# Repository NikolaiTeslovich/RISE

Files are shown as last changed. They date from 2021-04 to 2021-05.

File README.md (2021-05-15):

<h1 align="center">
  The Rocket Lab Initiative — RISE
</h1>

<p align="center">
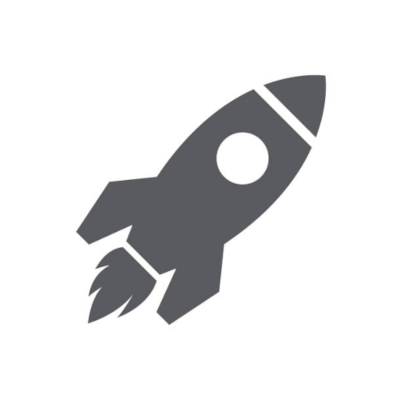
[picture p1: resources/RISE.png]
  
</p>

<p align="center">
  <a href="https://github.com/NikolaiTeslovich/RISE/blob/main/LICENSE">
    
  </a>
</p>

<p align="center">
  A payload that collects data and video throughout the flight of a model rocket.
</p>

# To do

- find appropriate camera resolution and framerate, [here's a helpful article](https://picamera.readthedocs.io/en/release-1.10/fov.html)
  - the spycam is the same as the picamera v1
  - does this affect the rate of data collection?
- Error encountered involving duplicate values with the data collections for the index
  - Meaning that 200 and 201 have the same time value, and are duplicates

# Breakdown of the code

1. First it imports the packages, sets up the sensors over I2C, and starts recording video.
2. Creates a new directory to put the data and video into, to prevent overwriting any data.
    - If no data directories exist, create the `data1` directory.
    - If the `data1` directory already exists, create the `data2` directory, etc.
3. Waits until the `delay_time` is over to collect data from the sensors as fast as possible using a [NumPy](https://numpy.org/) array over the `record_time` interval.
    - This comes out to about 40 measurements/sec compared to ~10 measurements/sec if I had used [pandas](https://pandas.pydata.org/) dataframes.
4. Every so many rows defined by the `iters` variable, dump the data into a csv and wipe the array.
    - This is done for bullet-proofness, so that if the payload breaks, data up to that point is saved.
    - The save time is only about ~0.1s.
5. When the `record_time` is over, the last of data is saved into a csv, and the camera stops recording.
6. All of the temporary csv files are merged into one `merged.csv` through the use of a dataframe (I found pandas the easiest way to do this).

**Note**. If your data gets corrupted for some reason, for example due to a random power out, run this command in the repo directory:

```
find .git/objects/ -size 0 -exec rm -f {} \; && git fetch origin
```

# Payload instructions

## Disclaimer

This is by far not the easiest thing to assemble, so if you are not confident in you tweezer usage skills when ribbon cables are involved, I recommend cutting out a hole in the rocket and mounting the camera facing sideways rather than down.

## Making the Pi headless

*And I didn't just chop off its head.*

Headless means that no connections to the Pi other than power and the network are needed to use it, essentially like a server.

### Install the Operating System (Pi OS Lite)

Raspberry Pi Imager is an app to make installing the operating system on your SD card a breeze.

Download it below:

https://www.raspberrypi.org/software/

Then, plug in the SD card and flash it with **Raspberry Pi OS Lite**.

### Making the Pi work headlessly

Remove, then plug back in the SD card.

In a terminal window, run:

```
touch /Volumes/boot/ssh
```

This will make a file on the SD card called `ssh`, which will enable ssh on the Pi.

Next, let's add some wifi information by creating another file on the SD card:

```
touch /Volumes/boot/wpa_supplicant.conf
```

Open the file with a text editing utility like TextEdit or nano, and paste in the following, substituting `NETWORK-NAME` with your wifi name and `NETWORK-PASSWORD` with the wifi password:

```
country=US
ctrl_interface=DIR=/var/run/wpa_supplicant GROUP=netdev
update_config=1

network={
    ssid="NETWORK-NAME"
    psk="NETWORK-PASSWORD"
}
```

Save the changes to the file, and eject the SD from your computer. The Pi is ready for its first boot.

###  Connecting to the Pi over ssh

After waiting for a couple minutes (the first boot takes quite a bit of time), connect to the Pi with this command, substituting the `ipaddress` with the ip of the Pi, which you can get through your router:

```
ssh pi@ipaddress
```

The password for the pi user is `raspberry`.

Then, update the Pi:

```
sudo apt update && sudo apt upgrade -y
```

To exit the ssh session just type `exit`.

### Making the code run on startup

Create a cron job, and selected the `[1]` option to edit it in nano:

```
crontab -e
```

At the very bottom, add the following to run the script on startup:

```
@reboot python3 /home/pi/RISE/flightcode.py &
```

*Important*: be sure to leave a line below the text, or else it might not work.

Exit out of nano by pressing ctrl-X followed by Y to save the changes.

Now, with a reboot the script should work.

### Transferring the data from the Pi to your computer with scp

The -r option is used to copy a directory, while the -p option is used to preserve file modification and access times.

Here's the general syntax:

```
scp -r -p remote_username@ip:/data_directory /local/directory
```

So for my use case, it would look like this (ip address omitted for obvious reasons):

```
scp -r -p pi@192.xxx.xxx.xxx:/home/pi/RISE/data1 ~/Downloads
```

The secure copy command connects to the pi and copies the directory at `/home/pi/RISE/data1/` to my computer's user Download directory `~/Downloads`.

## Sensor payload & camera assembly

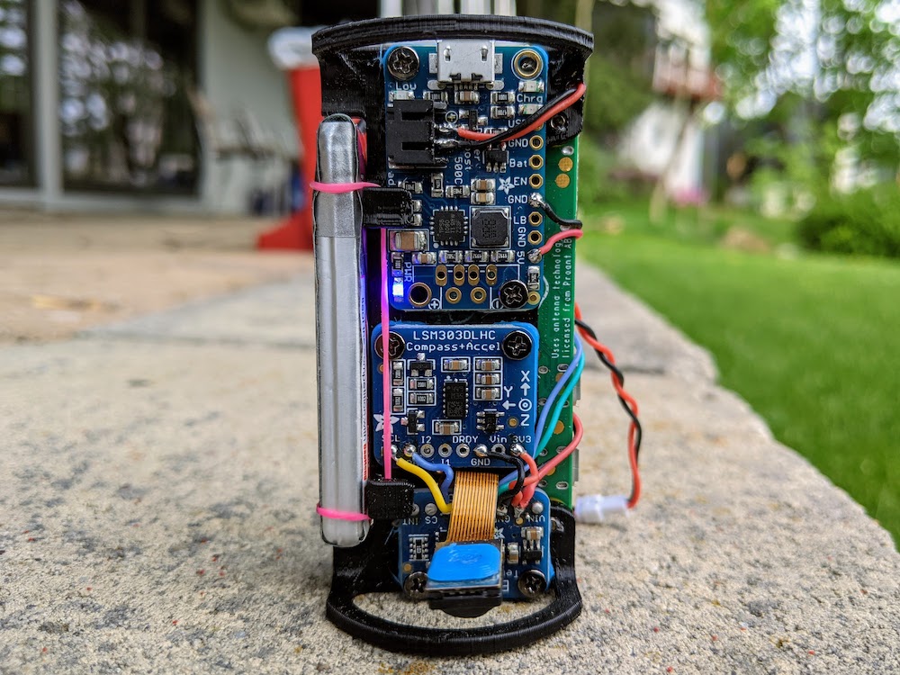
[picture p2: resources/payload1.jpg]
SensorPayload Side 1
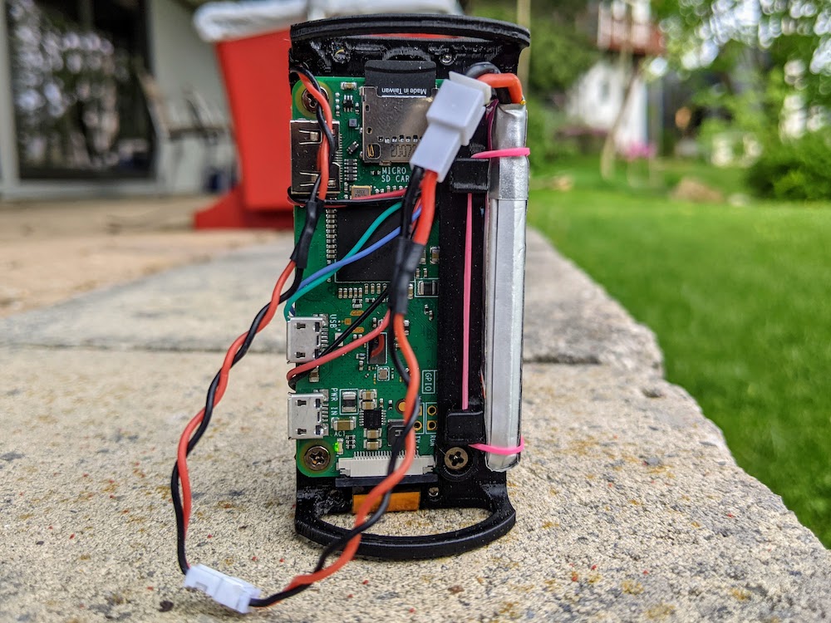
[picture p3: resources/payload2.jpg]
SensorPayload Side 2
|  |  |
| :---: | :---: |
|  Camera, sensor & voltage regulator  |  Raspberry Pi Zero W  |

### 3D printing

- STLs and Fusion 360 files located in the [files](/files) directory.
- Spacers were printed out of TPU
- Everything else was printed out of PLA at 215°C and 15% infill
  - Supports are only needed for the [SensorSkeleton](/files/SensorSkeleton.stl)

### Parts required

Just made of what I had lying around at the time. Feel free to change the hole sizes to fit your screw sizes through the included Fusion 360 files. Fusion 360 is free.

- 1x Raspberry Pi Zero W
- 1x PowerBoost 500C
- 1x LSM303DLHC
- 1x BMP338
- 1x [GNB 450mah 1s LiHV](https://www.amazon.com/PowerWhoop-Connector-Tinyhawk-Brushless-Inductrix/dp/B078Y3Y4ZZ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) - it's what I use in my super small FPV drones
- 10x 5mm M2.5 screws - from some old computer hard-drives
- 1x 10mm M3 screw
- 1x small rubber band
- 1x printed parts (obviously)

### Things to keep in mind

The screws tap into the plastic, so **do not** over-tighten them. Other than that, assembly should be pretty self-explanatory.

Also, make sure that the battery polarity matches the polarity of the PowerBoost 500C JST connector. The one on the GNB 450mah 1s is reversed. Or else, this will happen.

  > *magic smoke will come out*.

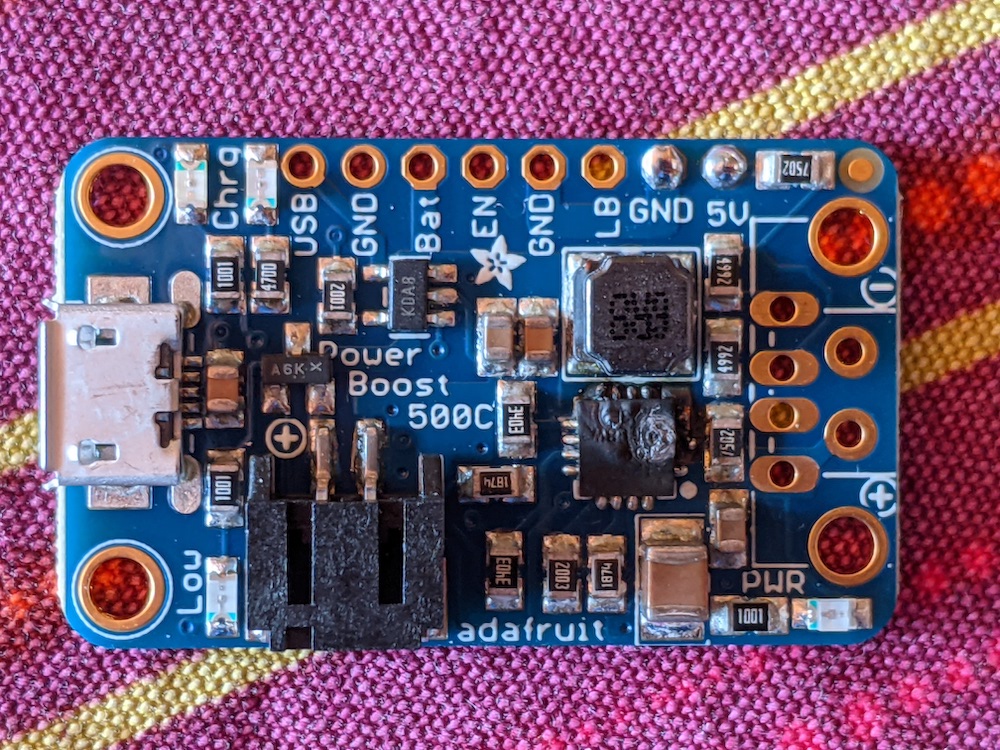
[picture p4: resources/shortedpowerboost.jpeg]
ShortedPowerBoost


# Some beautiful photographs

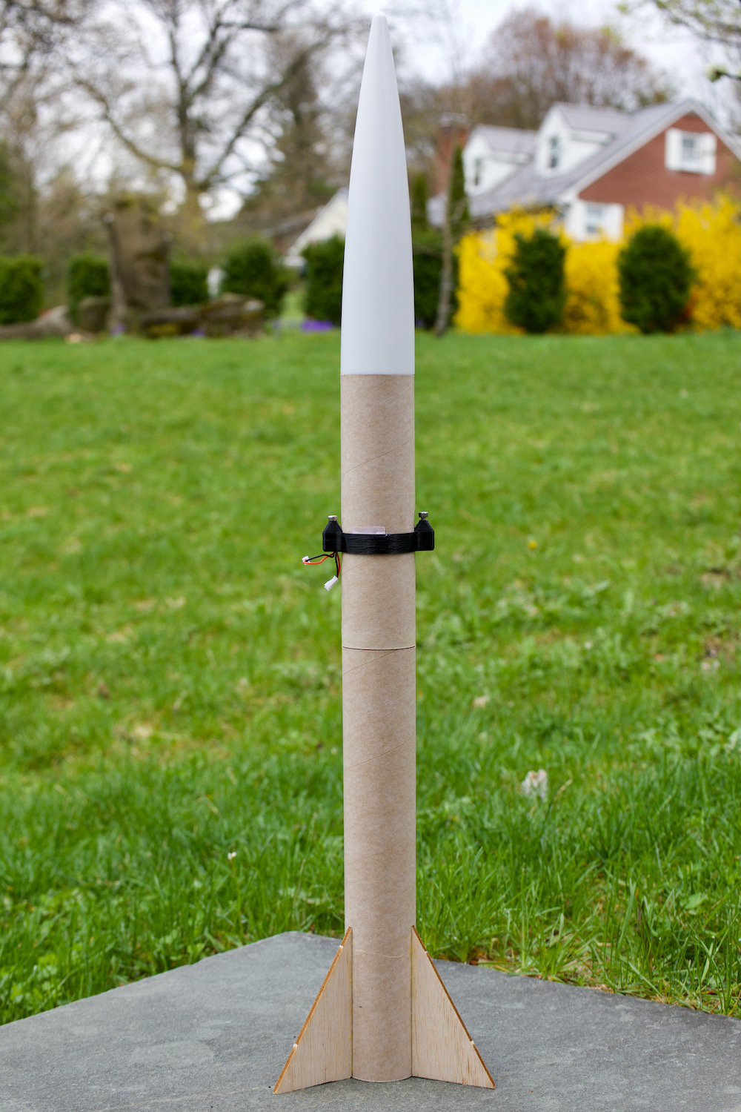
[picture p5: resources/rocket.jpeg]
Rocket
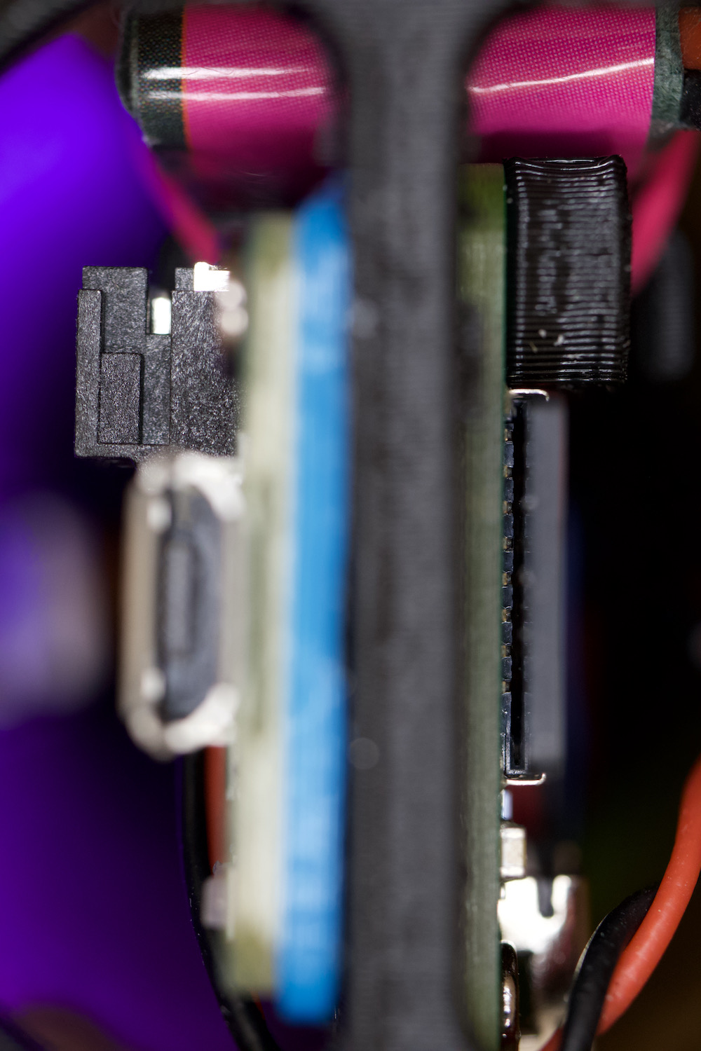
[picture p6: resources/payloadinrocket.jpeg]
Payload inside rocket
|  |  |
| :---: | :---: |
|  The rocket  |  Payload in the rocket  |

Last but not least, here is the external camera:

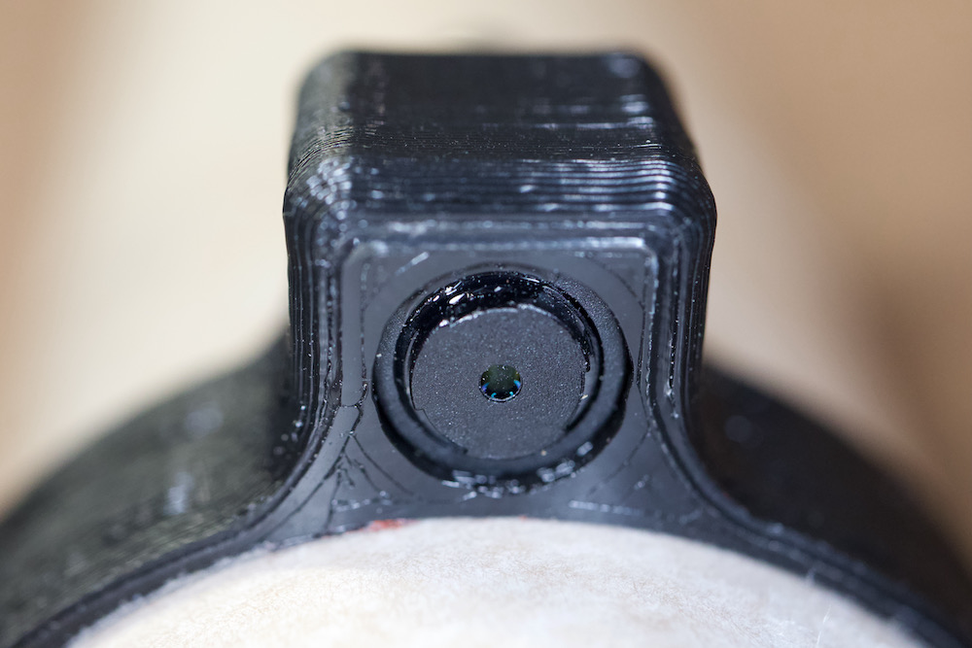
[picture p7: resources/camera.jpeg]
Camera mounted externally


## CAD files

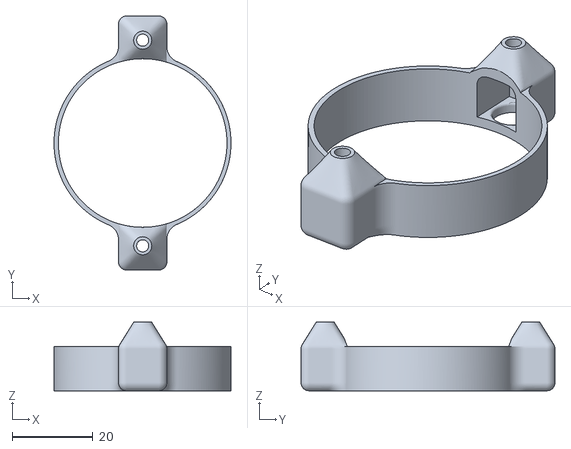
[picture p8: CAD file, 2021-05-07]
files/CameraMount.stl
43.9 x 63.0 x 17.0

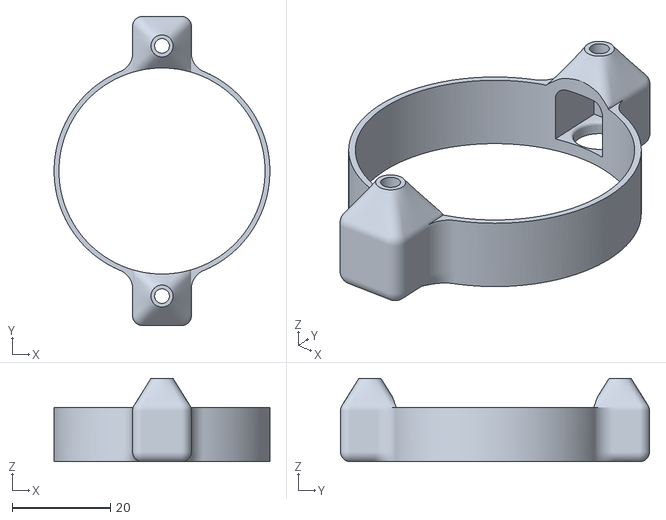
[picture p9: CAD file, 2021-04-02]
files/CameraMount_WiderDiameter.stl
44.0 x 63.0 x 17.0

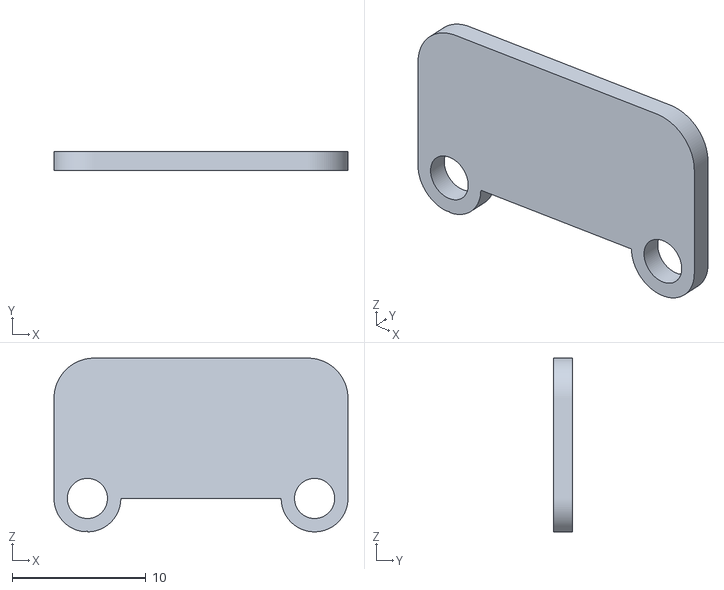
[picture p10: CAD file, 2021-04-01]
files/BMP338Spacer.stl
22.0 x 1.40 x 13.0

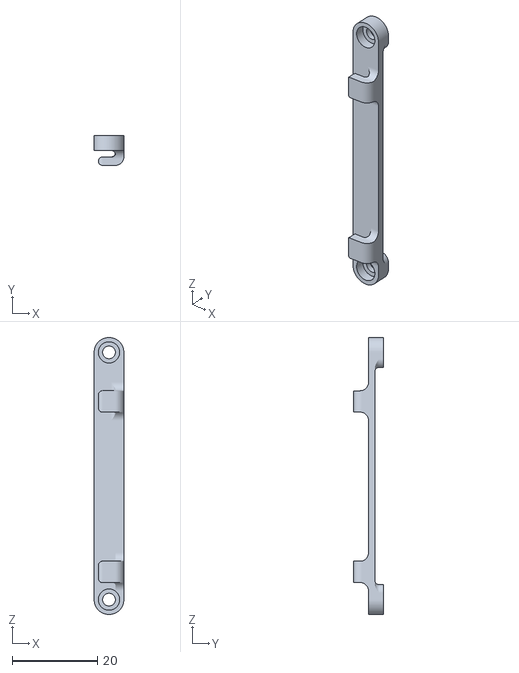
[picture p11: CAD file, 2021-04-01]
files/BatteryHolder.stl
7.00 x 7.00 x 65.0

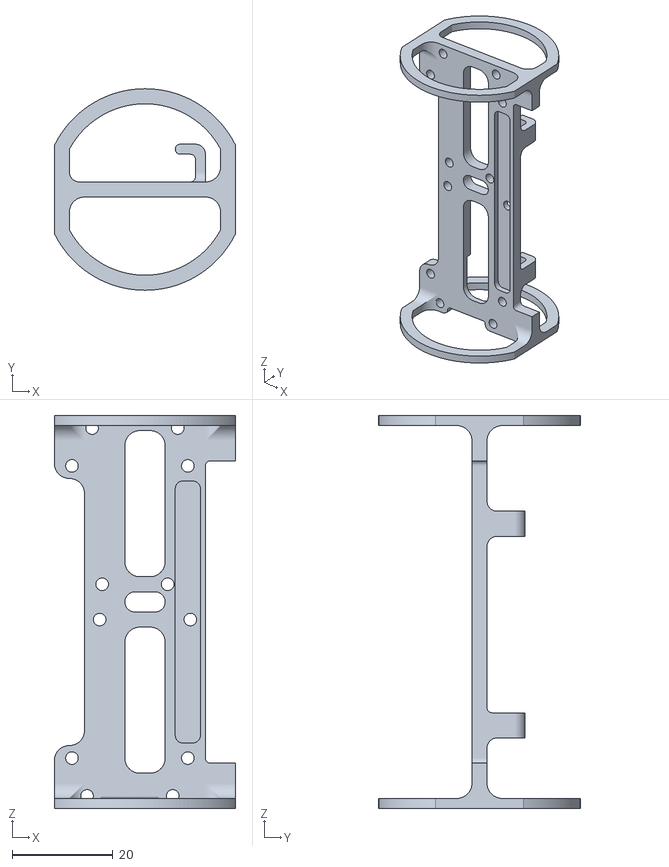
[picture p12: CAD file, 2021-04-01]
files/SensorSkeleton.stl
36.0 x 40.0 x 78.0

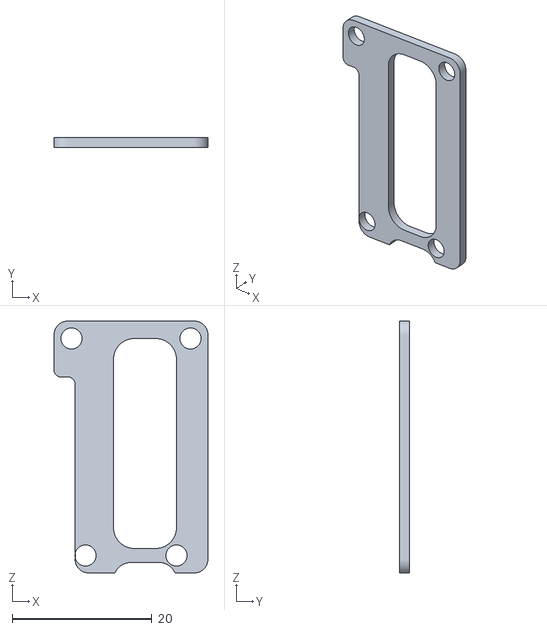
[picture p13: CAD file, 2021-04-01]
files/PowerBoostSpacer.stl
22.0 x 1.40 x 36.0

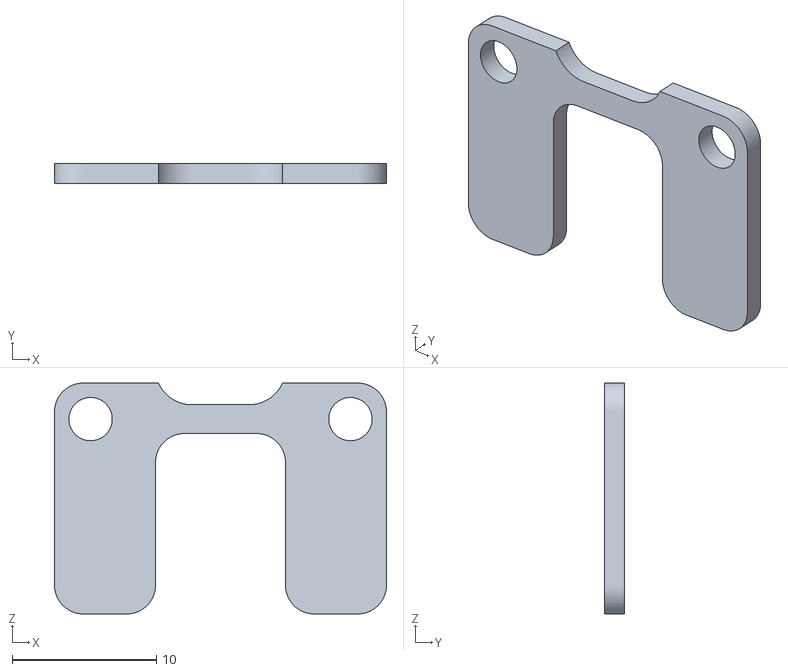
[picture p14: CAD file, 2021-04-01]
files/LSM303Spacer.stl
23.0 x 1.40 x 16.0

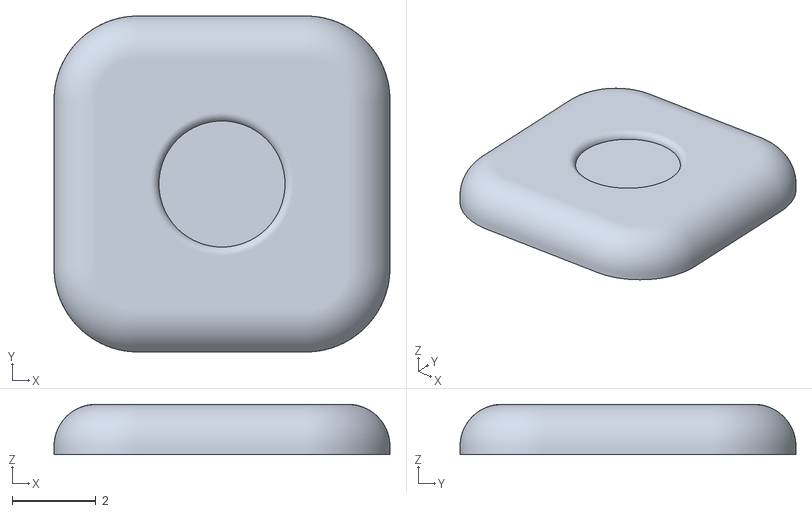
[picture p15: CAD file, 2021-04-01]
files/CameraScrewSpacer.stl
8.00 x 8.00 x 1.20

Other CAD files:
files/CameraMount.f3d
files/SensorMount.f3d

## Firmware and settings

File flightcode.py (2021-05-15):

import os
import glob
import numpy as np
import board
import busio
import adafruit_bmp3xx
import adafruit_lsm303_accel
import adafruit_lsm303dlh_mag
import time
import picamera
import pandas as pd

# Important parameters that can be altered
delay_time = 10
record_time = 60
# How many rows are data are in each temporary file
iters = 200

# Set up I2C and sensors
i2c = busio.I2C(board.SCL, board.SDA)
bmp = adafruit_bmp3xx.BMP3XX_I2C(i2c)
accel = adafruit_lsm303_accel.LSM303_Accel(i2c)
mag = adafruit_lsm303dlh_mag.LSM303DLH_Mag(i2c)

# Make the directory data2 if data1 exists, or data1 if no data directories exist
main_dir = os.listdir('/home/pi/RISE')
names = np.array([0])
for name in main_dir:
    if name.startswith('data'):
        name = np.array([name[4:]]).astype(np.int)
        names = np.append(names, name, axis=0).astype(np.int)
data_dir = f'/home/pi/RISE/data{np.max(names) + 1}'
os.mkdir(data_dir)
print('made directory at ' + data_dir)

# Set up camera stuff
### MAYBE ALSO ITERATE THE CAMERA RECORDINGS ###
### Format the recordings somehow ###
cam = picamera.PiCamera() #intialize camera
cam.resolution = (640, 480)
cam.framerate = 60
cam.start_recording(data_dir + '/' + 'video.h264') #start recording and name video file

# Define the time parameters
start_time = time.time()
i = 0

# Define the function to save a temporary file
def saveTempFile():
    # the formatting (the '{:03}') allows for up to 999 temp files
    file = open(data_dir + '/data' + '{:03}'.format(int(i / iters)) + '.csv', "w")
    np.savetxt(data_dir + '/data' + '{:03}'.format(int(i / iters)) + '.csv', datas, delimiter=",")
    file.close()

# Define one row of the array
datas = np.array([[0, 0, 0, 0, 0, 0, 0, 0, 0]])
# The data collection loop
while time.time() - start_time < delay_time + record_time:
    # Update elapsed time with every run
    elapsed_time = time.time() - start_time
    # Skip everything else if we're still in the delay period
    if elapsed_time < delay_time:
        continue
    # Append data to the array
    data = np.array([[(elapsed_time - delay_time), bmp.temperature, bmp.pressure,
                 accel.acceleration[0], accel.acceleration[1], accel.acceleration[2],
                 mag.magnetic[0], mag.magnetic[1], mag.magnetic[2]]])
    datas = np.append(datas, data, axis=0)
    i += 1
    # Save the data every so often
    if ((i + 1) % iters) == 0:
        #TESTING
        #test_time = time.time()
        saveTempFile()
        # Wipe the array to keep the same save time
        datas = np.array([[]])
        datas = np.array([[(elapsed_time - delay_time), bmp.temperature, bmp.pressure,
                 accel.acceleration[0], accel.acceleration[1], accel.acceleration[2],
                 mag.magnetic[0], mag.magnetic[1], mag.magnetic[2]]])
        #testing
        #print("--- %s seconds to save data ---" % (time.time() - test_time))
# Save the last bit of data after the final loop
saveTempFile()

# Stop the camera recording
cam.stop_recording()

# Make a massive, beautiful csv file at the end with all of the data
all_files = sorted(glob.glob(data_dir + '/' + '*.csv'))
df_from_each_file = (pd.read_csv(f, sep=',', header=None,
                                 names=['time','temperature','pressure',
                                        'acc_x','acc_y','acc_z',
                                        'mag_x','mag_y','mag_z']) for f in all_files)
df_merged = pd.concat(df_from_each_file, axis=0, ignore_index=True)

# a potential fix to a bug
#x = range(0, len(df_merged), 200)

#for n in x:
  #df_merged = df_merged.iloc[n:, :]

# Remove the first row, since the data is off for some reason
# df_merged = df_merged.iloc[1: , :]
# Write all of the data to to merged.csv
df_merged.to_csv(data_dir + '/' + 'merged.csv')
# Print done
print('done')
# Exit the program
exit()

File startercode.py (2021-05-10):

import pandas
import board
import busio
import adafruit_bmp3xx
import adafruit_lsm303_accel
import adafruit_lsm303dlh_mag
##### let's add in some extra functionality #####
import time #time package (if you want to use the sleep command and/or keep track of time)
import picamera #running the spycamera while gathering datas

##### set up I2C and sensors #####
i2c = busio.I2C(board.SCL, board.SDA)
bmp = adafruit_bmp3xx.BMP3XX_I2C(i2c)
accel = adafruit_lsm303_accel.LSM303_Accel(i2c)
mag = adafruit_lsm303dlh_mag.LSM303DLH_Mag(i2c)

##### let's say we want to make a list of all sensor measurements and alo keep track of time... #####
df = pandas.DataFrame(columns=['time','temperature','pressure',
			       'acc_x','acc_y','acc_z',
			       'mag_x','mag_y','mag_z'])
#set up a DataFrame with columns time, for temp, pressure, 3 columns for acceleraton and 3 for magnetometer

# Set up camera stuff.
cam = picamera.PiCamera() #intiialize camera
cam.resolution = (640,800) #set camera resolution
cam.start_recording('test_video.h264') #start recording and name video file

# Define start time, delay, and total elapsed time.
start_time = time.time()
delay_time = 100
record_time = 500

# print('Start')

elapsed_time = time.time() - start_time
while elapsed_time < delay_time + record_time:
    # Update elapsed time.
    elapsed_time = time.time() - start_time
    # Skip everything else if we're still in delay period.
    if elapsed_time < delay_time:
        continue
    # Otherwise, append data to dataframe.
    df = df.append({'time':elapsed_time,
                    'temperature':bmp.temperature,
	  	    		'pressure':bmp.pressure,
		    		'acc_x':accel.acceleration[0],
	            	'acc_y':accel.acceleration[1],
		    		'acc_z':accel.acceleration[2],
		    		'mag_x':mag.magnetic[0],
	            	'mag_y':mag.magnetic[1],
		    		'mag_z':mag.magnetic[2]},
		    		ignore_index=True)

# Stop camera recording.
cam.stop_recording()

# Save data.
df.to_csv('test_data.csv')

# Specific to testing this code. Let's you know it's done.
total_elapsed = time.time() - start_time
print(total_elapsed)

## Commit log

2020-12-14 added the code
    [data.csv]
2021-01-11 testing accelerometer and magnetomer sensor
    [data.csv]
2021-01-25 organizes into directories
    [data.csv]
2021-01-25 made a temp sensor test script
2021-01-25 trying out all the sensors
2021-02-08 camera testing
2021-02-08 camera code
2021-03-08 cleaned up repo
    [data.csv, temp.csv, time_temp_press_accel_mag.csv]
2021-03-30 added STLs
    [RISE_V7.stl, SensorSpacerLRG.stl, SensorSpacerSML.stl]
2021-03-30 cleaned up directories
    [SensorSpacerLRG.stl, SensorSpacerSML.stl, SkeletalFairing.stl]
2021-03-30 added Fusion 360 parts
    [RISE_SensorMount.f3d, SensorSpacerLRG.stl, SensorSpacerSML.stl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]
2021-03-31 found proper screw size
2021-03-31 added updated files
    [RISE_Cam_V5.stl, RISE_Spacer_1.stl, RISE_Spacer_2.stl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]
2021-04-01 managing files
    [RISE_Cam_V5.stl, RISE_SensorMount.f3d, RISE_Spacer_1.stl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]
2021-04-01 added latest files
    [CameraMount.f3d, RISE_CamSpacer_V3.stl, RISE_Holder_V2.stl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]
2021-04-01 added the camera mount
    [RISE_Cam_V7.stl]
2021-04-01 enhanced file names
    [BMP338Spacer.stl, BatteryHolder.stl, CameraMount.stl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]
2021-04-02 revised camera mount
    [CameraMount.f3d, CameraMount.stl]
2021-04-05 found the right motor
2021-04-06 testing code
    [rocketdata.csv]
2021-04-12 added a wider diameter version for messy printers
    [CameraMount.stl, CameraMount_WiderDiameter.stl]
2021-05-03 added simulation data
    [F50T-6_Simulation.csv]
2021-05-07 greatly improved code
    [data.csv, rocketdata.csv]
2021-05-07 made flightcode a program
    [F50T-6_Simulation.csv, data1.csv, data10.csv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]
2021-05-07 improved program
    [data.csv, data1.csv, data10.csv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]
2021-05-07 data is recorded into the data directory
    [data.csv]
2021-05-07 fixed corrupt objects
    [data.csv]
2021-05-09 finalized other program
    [data.csv, data0.csv, data1.csv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]
2021-05-09 renamed files
    [data0.csv, data1.csv, data10.csv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]
2021-05-09 added camera parameters
2021-05-09 figured out program
    [data0.csv, data1.csv, data2.csv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]
2021-05-09 backed up latest version of jupyter notebook
    [data018.csv, data019.csv, data020.csv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]
2021-05-09 some minor changes
    [data0.csv, data000.csv, data001.csv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]
2021-05-09 graphed some data
    [data000.csv, data001.csv, data002.csv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]
2021-05-09 cleaned up
    [data000.csv, data001.csv, data002.csv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]
2021-05-10 removed unnecessary files
    [merged.csv, newfile.csv]
2021-05-10 started writing user guide
    [simulation.csv]
2021-05-10 made some data
    [data000.csv, data001.csv, data002.csv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]
2021-05-12 removed useless script
    [data000.csv, data001.csv, data002.csv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]
2021-05-15 enabled camera
2021-05-15 cleaning up
    [merged.csv]
2021-05-16 rocket launch was :)!
    [merged.csv]

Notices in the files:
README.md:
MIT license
